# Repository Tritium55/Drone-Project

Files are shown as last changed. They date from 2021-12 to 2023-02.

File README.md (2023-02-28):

# Drone-Project
Project Zora - Indoor Drone With Return Home Function

## Used Parts

| Part | Quantity | Link to Manufacturer | Pricepoint |
| ---- |:---:|:---:|:---:|
| Arduino Nano | 1 | [store.arduino.cc](https://store.arduino.cc/collections/most-popular/products/arduino-nano "Arduino Nano") | 10€ |
| PCB or Breadboard | 1 | *order from e.g.* [*JLCPCB*](https://jlcpcb.com/) *or* [*PCBWay*](https://www.pcbway.com/) *in 2 oz thickness* | 15€ + shipping |
| Brushless Motor | 4 | [BETAFPV 1103 8000KV](https://betafpv.com/products/1103-brushless-motors?variant=14735142682668 "BETAFPV 1103 8000KV") | 40€ |
| ESC | 4 | [FVT LittleBee BLHeli_S 2-6S 20A ESC](https://de.aliexpress.com/item/32979616081.html?gatewayAdapt=glo2deu&spm=a2g0o.order_list.0.0.21ef5c5fJXpupL "4x ESC") | 25€ |
| 3 inch Propeller | 4 | [BETAFPV HQ 3030 3-Blade Prop](https://betafpv.com/products/hq-3030-2-blade-propellers-1-5-shaft-16-pcs?variant=29701772673068 "Propeller Set of 16") | 2,25€ per set of 4 |
| Receiver | 1 | [FlySkky RX2A Pro v1 2.4GHz](https://micro-squad.com/en/product/flysky-rx2a-pro-v1-2-4ghz-micro-empfaenger/ "Micro Receiver") | 17€ |
| Gyroscope | 1 | [GY-521 MPU-6050](https://www.amazon.de/gp/product/B07TKLYBD6/ref=ppx_yo_dt_b_asin_title_o01_s00?ie=UTF8&th=1 "3-Axis Gyroscope") | 5€ |
| Infrared Sensor | 1 | | |
| Ultrasonic Sensor | 1 | [HC-SR04](https://www.amazon.de/-/en/dp/B07TKVPPHF/ref=twister_B07ZRQQ46L?_encoding=UTF8&psc=1 "Ultrasonic Sensor Module") | 4€ |
| 16V 470µF Capacitor | 1 | | |
| 3S LiPo Battery | 1 | [BETAFPV 450mAh 3S 75C LiPo Battery](https://betafpv.com/collections/batt-3s/products/450mah-3s-75c-lipo-battery-2pcs "LiPo Battery") | 14€ each |

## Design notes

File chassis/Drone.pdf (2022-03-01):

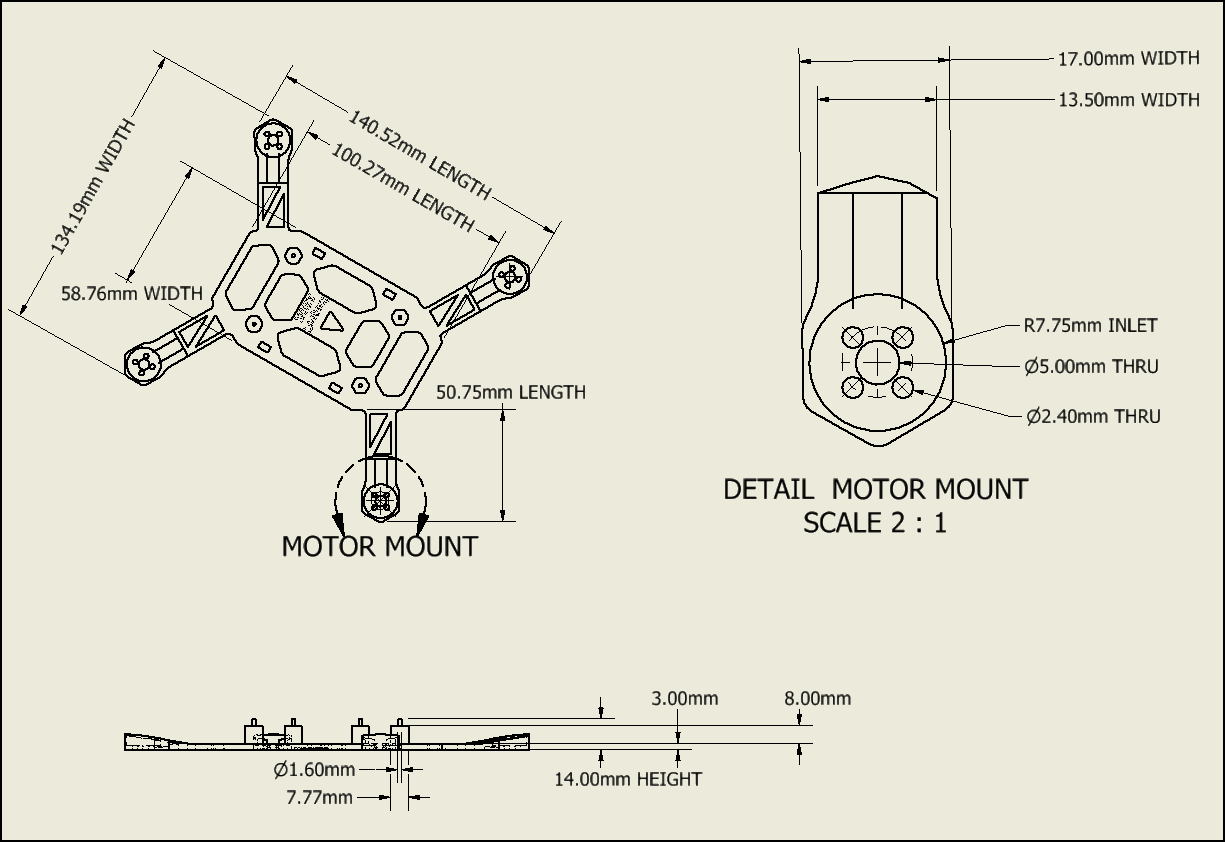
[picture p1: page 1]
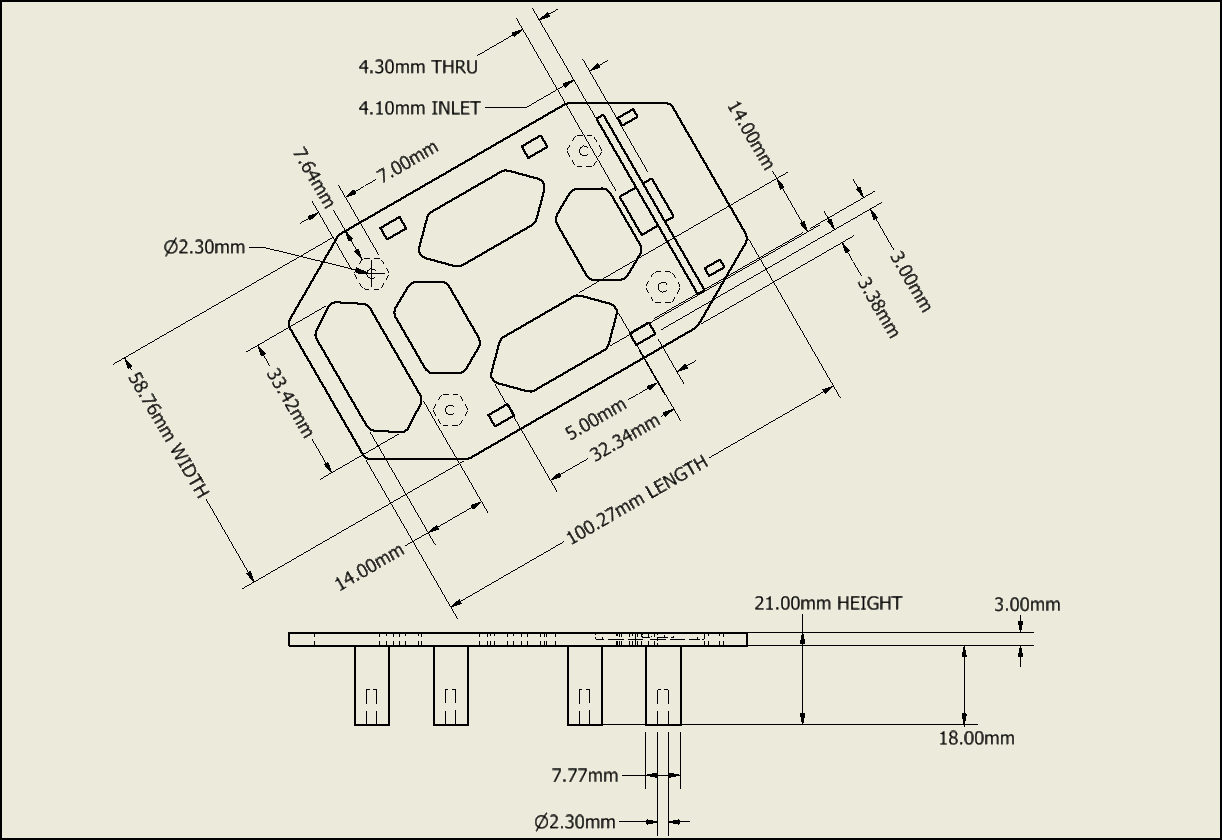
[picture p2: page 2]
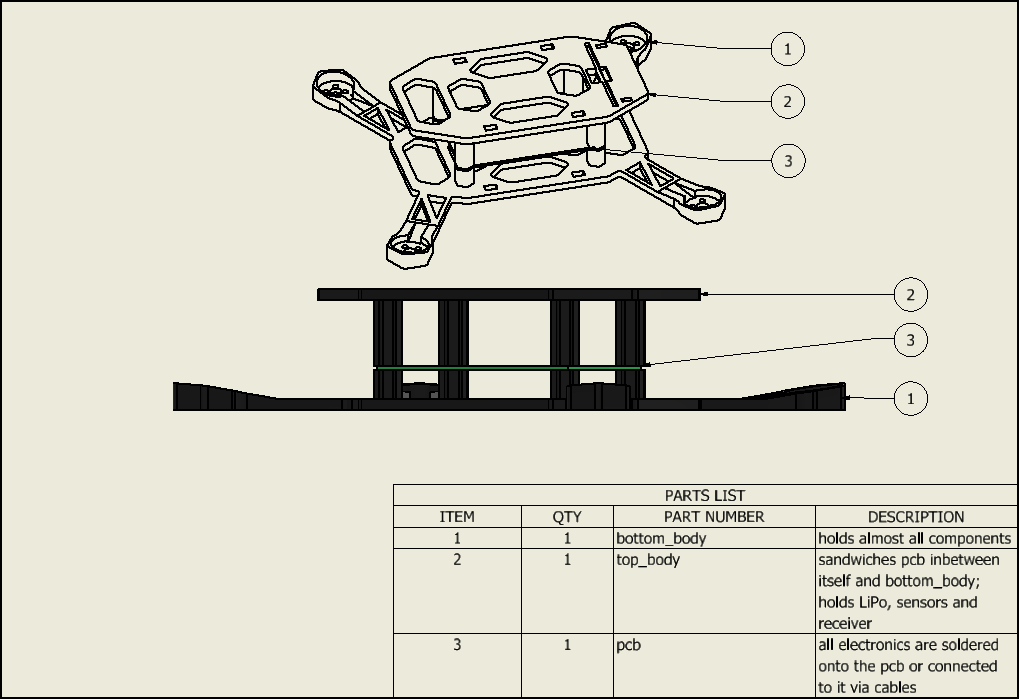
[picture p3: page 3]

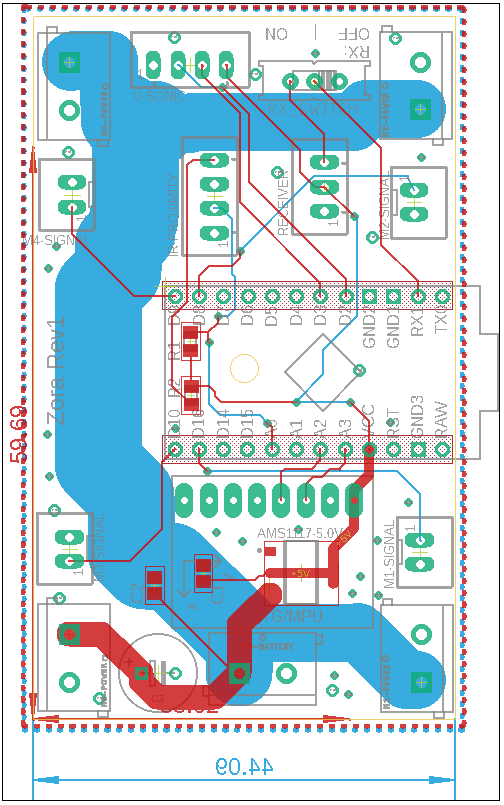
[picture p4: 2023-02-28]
PCB/pcb.png

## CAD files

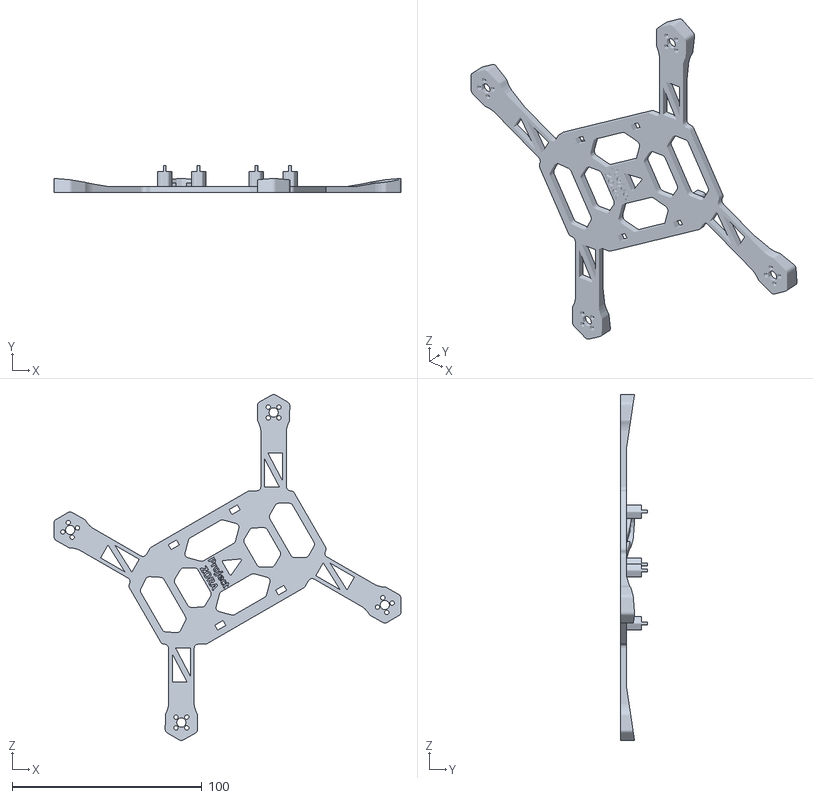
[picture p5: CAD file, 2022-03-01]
chassis/Drone_Case_Bottom.stl
182.9 x 14.0 x 182.3

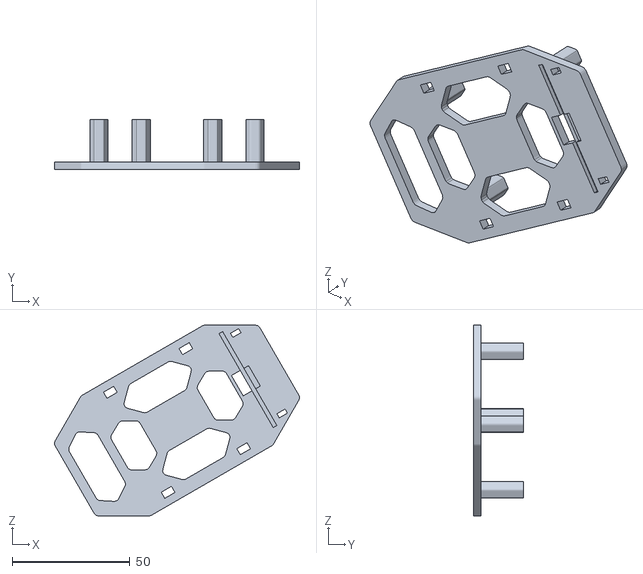
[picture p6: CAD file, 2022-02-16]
chassis/Drone_Case_Top.stl
103.9 x 21.0 x 80.9

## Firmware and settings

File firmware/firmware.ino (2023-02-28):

#include "./return_home.h"
#include "./motor_control.h"
#include "./IBUS_Receiver.h"

//all user settings are included from this file
#include "./settings.h"


//uncomment next line for channel debugging
//#define SERIAL_WRITE_CHANNEL_OUT

//uncomment next line for pulse_map debugging
//#define SERIAL_WRITE_PULSE_MAP

//uncomment next line for temp_speed debugging
//#define SERIAL_WRITE_TEMP_SPEED

#define rh rclass
#define IBus IBus_Receiver

//create brushless motors
BrushlessMotor m1(BrushlessNr1);
BrushlessMotor m2(BrushlessNr2);
BrushlessMotor m3(BrushlessNr3);
BrushlessMotor m4(BrushlessNr4);


IBus receiver;                          //receiver init
Channels1to4_read Channels1to4;         //for return value of channel read

int pulse_map_CH1, pulse_map_CH2, pulse_map_CH3, pulse_map_CH4;


//maps all read values from function void readChannels
void mapReads(int lowChannel, int highChannel);


//returns 0, 1 or 2 depending on which value is currently mapped on pulse_map_CH6
int evaluateCh6(int val) {
  if (val == 1500) return 0;
  else if (val == 2000) return 1;
  else if (val == 1750) return 2;
}

//bool rh.returnHome(void);
//TODO: complex function which returns the drone home


//writes all motors
void write_motors(void) {
  m1.writeMotor();
  m2.writeMotor();
  m3.writeMotor();
  m4.writeMotor();
}

//resets speed of all motors
void reset_speed(void) {
  m1.setSpd(0);
  m2.setSpd(0);
  m3.setSpd(0);
  m4.setSpd(0);
}

//power off for drone
void poweroff() {
  reset_speed();
  write_motors();
  exit(0);
}

void setup() {
  //sensor_setup();                 //setups all sensors needed for return_home

  IBus_Receiver_Init();
  
  m1.BrushlessMotorInit();
  m2.BrushlessMotorInit();
  m3.BrushlessMotorInit();
  m4.BrushlessMotorInit();

  delay(5000);                      //delay for ESC init
}

int max_of_4(int a, int b, int c, int d) {
  int temp1 = max(a, b);
  int temp2 = max(c, d);
  return max(temp1, temp2);
}


int temp_spd1, temp_spd2, temp_spd3, temp_spd4;
void loop() {
  switch (evaluateCh6(receiver.readChannel6())) {
    case 0: break;
    case 1: poweroff();
            break;
    case 2: break;                            //change later for return home
  }

  temp_spd1 = temp_spd2 = temp_spd3 = temp_spd4 = 0;

  Channels1to4 = receiver.readChannels1to4();
  pulse_map_CH1 = map(Channels1to4.arr[0], RECEIVER_RANGE_MIN, RECEIVER_RANGE_MAX, CH_1_2_4_SENS_LOW, CH_1_2_4_SENS_HIGH);
  pulse_map_CH2 = map(Channels1to4.arr[1], RECEIVER_RANGE_MIN, RECEIVER_RANGE_MAX, CH_1_2_4_SENS_LOW, CH_1_2_4_SENS_HIGH);
  pulse_map_CH3 = map(Channels1to4.arr[2], RECEIVER_RANGE_MIN, RECEIVER_RANGE_MAX, CH_3_MIN_THROTTLE, CH_3_MAX_THROTTLE);
  pulse_map_CH4 = map(Channels1to4.arr[3], RECEIVER_RANGE_MIN, RECEIVER_RANGE_MAX, CH_1_2_4_SENS_LOW, CH_1_2_4_SENS_HIGH);

  #ifdef SERIAL_WRITE_PULSE_MAP
  Serial.print("pulse_map_CH1: ");
  Serial.println(pulse_map_CH1);
  Serial.print("pulse_map_CH2: ");
  Serial.println(pulse_map_CH2);
  Serial.print("pulse_map_CH3: ");
  Serial.println(pulse_map_CH3);
  Serial.print("pulse_map_CH4: ");
  Serial.println(pulse_map_CH4);

  delay(200);   //delay for printing
  #endif //SERIAL_WRITE_PULSE_MAP

  #ifdef SERIAL_WRITE_CHANNEL_OUT
  Serial.print("Channel 1: ");
  Serial.println(Channels1to4.arr[0]);
  Serial.print("Channel 2: ");
  Serial.println(Channels1to4.arr[1]);
  Serial.print("Channel 3: ");
  Serial.println(Channels1to4.arr[2]);
  Serial.print("Channel 4: ");
  Serial.println(Channels1to4.arr[3]);

  delay(200);   //delay for printing
  #endif //SERIAL_WRITE_CHANNEL_OUT

  //add spd of CH1 to motors      ROLL
  if (pulse_map_CH1 > 0) {
    temp_spd3 += pulse_map_CH1;
    temp_spd4 += pulse_map_CH1;
  }
  else {  //if(pulse_map_CH1<0)
    temp_spd1 += -pulse_map_CH1;
    temp_spd2 += -pulse_map_CH1;
  }


  //add spd of CH2 to motors      PITCH
  if (pulse_map_CH2 > 0) {
    temp_spd1 += pulse_map_CH2;
    temp_spd3 += pulse_map_CH2;
  }
  else {  //if(pulse_map_CH<0)
    temp_spd2 += -pulse_map_CH2;
    temp_spd4 += -pulse_map_CH2;
  }


  //add spd of CH4 to motors      YAW
  if (pulse_map_CH4 > 0) {
    temp_spd1 += pulse_map_CH4;
    temp_spd4 += pulse_map_CH4;
  }
  else {  //if(pulse_map_CH<=0)
    temp_spd2 += -pulse_map_CH4;
    temp_spd3 += -pulse_map_CH4;
  }


  //add spd of CH3 to motors      THROTTLE
  int temp_comparison = max_of_4(temp_spd1, temp_spd2, temp_spd3, temp_spd4);
  if (temp_comparison + pulse_map_CH3 >= CH_3_MAX_THROTTLE) {                   //bounds detection to not surpass motor spd limit
    int temp_val = (temp_comparison + pulse_map_CH3) - CH_3_MAX_THROTTLE;
    temp_spd1 += pulse_map_CH3 - temp_val;
    temp_spd2 += pulse_map_CH3 - temp_val;
    temp_spd3 += pulse_map_CH3 - temp_val;
    temp_spd4 += pulse_map_CH3 - temp_val;
  }
  else {
    temp_spd1 += pulse_map_CH3;
    temp_spd2 += pulse_map_CH3;
    temp_spd3 += pulse_map_CH3;
    temp_spd4 += pulse_map_CH3;
  }

  #ifdef SERIAL_WRITE_TEMP_SPEED
  Serial.print("temp_spd1: ");
  Serial.println(temp_spd1);
  Serial.print("temp_spd2: ");
  Serial.println(temp_spd2);
  Serial.print("temp_spd3: ");
  Serial.println(temp_spd3);
  Serial.print("temp_spd4: ");
  Serial.println(temp_spd4);

  delay(200);
  #endif //SERIAL_WRITE_TEMP_SPEED

  //write speeds to ESC's and set speeds to 0 afterwards
  m1.setSpd(temp_spd1);
  m2.setSpd(temp_spd2);
  m3.setSpd(temp_spd3);
  m4.setSpd(temp_spd4);
  write_motors();
  reset_speed();                    //sets speed of all motors to 0
}

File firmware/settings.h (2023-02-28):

#ifndef settings_h
#define settings_h

//! USER SETTINGS BEGIN HERE

//define Serial Input for IBUS Receiver Output
#define SERIAL_INPUT Serial1

//define pins of all 4 brushless motors
#define BrushlessNr1 16
#define BrushlessNr2 8
#define BrushlessNr3 10
#define BrushlessNr4 9

//define pins of GY-521 Gyroscope
#define GY521_SCL A3
#define GY521_SDA A2

//define sensitivity of all channels exept THROTTLE
#define CH_1_2_4_SENS_LOW -200
#define CH_1_2_4_SENS_HIGH 199

//define range of THROTTLE
#define CH_3_MIN_THROTTLE 0
#define CH_3_MAX_THROTTLE 1000

//ESC PWM RANGE
#define ESC_RANGE_MIN 1000
#define ESC_RANGE_MAX 2000

//RECEIVER PWM RANGE
#define RECEIVER_RANGE_MIN 1000
#define RECEIVER_RANGE_MAX 2000


//! USER SETTINGS END HERE


#endif  //settings_h

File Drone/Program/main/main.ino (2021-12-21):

#define CH1 1
#define CH2 2
#define CH3 3
#define CH4 4
#define CH6 6

int pulse_read_CH1, pulse_read_CH2, pulse_read_CH3, pulse_read_CH4;
int pulse_read_CH6;
int pulse_map_CH1, pulse_map_CH2, pulse_map_CH3, pulse_map_CH4;
int pulse_map_CH6;

void readChannels(int lowChannel, int highChannel);
//reads all channels between lowChannel and highChannel including both and saves the read values to global vars
void writeMotors(void);
//converts mapped values and writes them to the ESC
void mapReads(int lowChannel, int highChannel);
//maps all read values from function void readChannels
int evaluateCh6(void);
//returns 0, 1 or 2 depending on which value is currently mapped on pulse_map_CH6
bool returnHome(void);
//complex function which returns the drone home

void setup() {
  // put your setup code here, to run once:

}

void loop() {
  // put your main code here, to run repeatedly:

}

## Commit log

2021-12-09 upload plans with creation of git-repository
    [battery_holder.stl, camera_holder.stl, lower_body.stl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]
2021-12-14 arduino read receiver
2022-01-04 esc data and tests
2022-01-21 motor arm prototype
    [motor_arm.0003.ipt, motor_arm.ipt]
2022-01-21 testing merge feature with motor_arm prototype
    [motor_arm.0003.ipt, motor_arm.ipt]
2022-01-23 esc differencies defined
2022-01-23 resize of motor arm with prototype test prints
    [first_prototype_of_motorarm_short.stl, motor_arm.0003.ipt, motor_arm.0009.ipt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]
2022-01-24 reupload the ipt files
    [motor_arm.0010.ipt, motor_arm.ipt]
2022-01-24 random rebasing going on
    [motor_arm.0003.ipt, motor_arm.ipt]
2022-01-24 clean up main branch
    [motor_arm.0003.ipt, motor_arm.ipt]
2022-01-25 adding motor_arm.ipt
    [motor_arm.ipt]
2022-01-30 bottom body almost done
    [bottom_body.0027.ipt, bottom_body.ipt, motor_arm.ipt]
2022-02-01 first prototype of bottom body
    [bottom_body.0027.ipt, bottom_body.0031.ipt, bottom_body.ipt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]
2022-02-04 modified README and addition of Arduino folder
2022-02-08 second prototype of bottom body
    [bottom_body.0031.ipt, bottom_body.0036.ipt, bottom_body.ipt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]
2022-02-08 third prototype of bottom_body
    [bottom_body.0036.ipt, bottom_body.0037.ipt, bottom_body.ipt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]
2022-02-08 esc control works
2022-02-12 redesign of bottom body to possibly solve thermal issues with motors
    [bottom_body.0038.ipt, bottom_body.0039.ipt, bottom_body.ipt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]
2022-02-13 top body first two prototypes
    [top_body.0007.ipt, top_body.ipt, top_body_first_prototype.stl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]
2022-02-14 top body and bottom body standof mods
    [bottom_body.0039.ipt, bottom_body.0041.ipt, bottom_body.ipt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]
2022-02-16 new resizeing for standoffs
    [bottom_body.0041.ipt, bottom_body.0042.ipt, bottom_body.ipt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]
2022-02-16 prop direction
2022-02-27 removing files of original design idea
    [battery_holder.stl, bottom_body.0042.ipt, bottom_body.ipt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]
2022-02-27 pushing stl files
    [Drone_Casing_Bottom.stl, Drone_Casing_Top.stl]
2022-02-27 random shit and uploading files
    [bottom_body.0042.ipt, bottom_body.ipt, bottom_body_fifth_prototype_without_guard.stl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]
2022-03-01 Drone case documentation
    [Drone_Case_Bottom.stl, Drone_Case_Top.stl, Drone_Casing_Bottom.stl]
2023-02-28 update from private repo after some time. still not up to date on chassis stl files.
    [Drone_Case_Bottom.stl, Drone_Case_Top.stl]
